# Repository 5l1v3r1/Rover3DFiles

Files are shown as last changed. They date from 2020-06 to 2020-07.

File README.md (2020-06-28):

<p align="justify"><b>
<font size="2">Tanım</font></b><font size="2"><br>
Bu bölümde projenin bir parçası olan, İnternet üzerinden kontrol edilecek ve üzerinde çeşitli görev yükü bulunacak olan model Mars Rover'a ait 3D yazıcı dosyaları yer almaktadır.
</font></p>
<p align="justify"><b><font size="2">Malzeme<br>
</font></b><font size="2"> Malzeme olarak istenilen renkte filament kullanılabilir. Çalışmalarda kullanılan filament türü PLA'dır. Dosyalar 180-220 Nozzle, 55-60 tabla sıcaklığında, %7 doluluk oranında basılabilir. Yüklenmiş/yüklenecek dosyalar *.stl formatında olup, kendi 3D yazıcınıza uygun bir 
dilimleyici programı kullanarak G-Code üretebilirsiniz. Kabin ve amortisör sistemleri destekli baskıya ihtiyaç duymaktadır.</font></p>

----------------------------------------------------------------

<b>Description: </b>

This section includes 3D printer files of the Mars Rover model, which will be controlled over the Internet and will have various tasks. 

<b>Materials: </b>

As a printing material, any preferred color of filament can be used. The type of filament used in the this project is PLA. Files can be printed with 180-220 Nozzle, 55-60 bed temperature, 7% fullness ratio. Files, which are already uploaded or will be uploaded, will be in *.stl format. So it will be possible to create G-Code suitable for your 3D printer by using an appropriate slicing program. Cabin and dashpot systems need supported printing.

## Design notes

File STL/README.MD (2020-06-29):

<p align="justify"><font size="2">
<b>Tekerlekler</b><br>
6 Adet yüzeyine tutunma çıkıntıları 
eklenmiş, 5 adet jant bağlantılı destek parçasına sahip, 100 mm çapında 
tekerlerden oluşmaktadır. Bir tekerin baskı süresi genel tip yazıcılarda 
yaklaşık olarak 6,5 saattir, toplamda teker başına yaklaşık 14.8 metre 44 gram 
filament harcanmaktadır. Teker mili yuvası standart 6V 250 RPM plastik dişli çift 
şaftlı motorlar için uygundur. Yapıştırma desteği için 1 mm esnek pay 
bırakılmıştır.</font></p>
<p align="justify"><b><font size="2">Tutucular</font></b><font size="2"><br>
Ana gövde ile tekerlek sistemini birleştiren kare 
şeklindeki parçadır. Rover üzerinde 3 adet bulunmaktadır. Bu malzemenin görevi; 
rover'e modüler bir yapı kazandırarak istenildiği gibi uzunluğun ve kullanım 
hacminin değiştirilmesine olanak sağlamak, farklı çap teker yapısının kolayca 
değiştirilebilmesine olanak sağlamaktır.&nbsp; Yaklaşık olarak 1 saat 23 dakika 
baskı süresinde 4 metre 12 gram filament&nbsp;harcanmaktadır.&nbsp;&nbsp;&nbsp; </font>
</p>
<p align="justify"><b><font size="2">Salıncak</font></b><font size="2"><br>
Tutucu, amortisör ve motor yatağı ile birlikte 
kullanılan ve teker yapısına arazinin durumuna göre dikey eksende esnek hareket 
sağlayan yapıdır. Rover üzerinde 6 adet yer almaktadır.</font></p>
<p align="justify"><b><font size="2">Amortisörler<br>
</font></b><font size="2">Aracın engebeli arazide sürüş stabilitesini arttırmak amacıyla 
kullanılan sistemdir. Yay sertliği ve malzemesi kullanıcı tarafından 
ayarlanabilir. Sistem iki adet birbirinin içine geçen parçadan oluşmaktadır, 
rover üzerinde toplamda 6 adet amortisör takımı vardır. Amortisör başına 
yaklaşık olarak 4 dakika baskı süresinde 1.51 metre 5 gram filament harcanmaktadır.</font></p>
<p align="justify"><font size="2"><b>Motor Yatağı</b><br>
Plastik dişli motoru sabitleyen ve taşıyan ve salıncağa bağlanan parçadır. 
Yaklaşık olarak 57 dakika baskı süresinde, 2,30 metre 7 gram filament harcanmaktadır. Parçanın destekli basılması önerilir.</font></p>

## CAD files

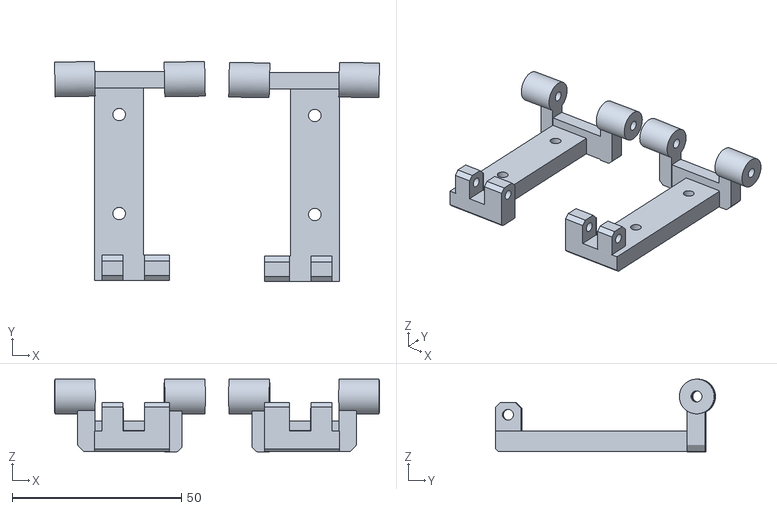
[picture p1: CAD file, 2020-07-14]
STL/Salincak-Suspensionx2-L-R.stl
96.0 x 65.0 x 21.5

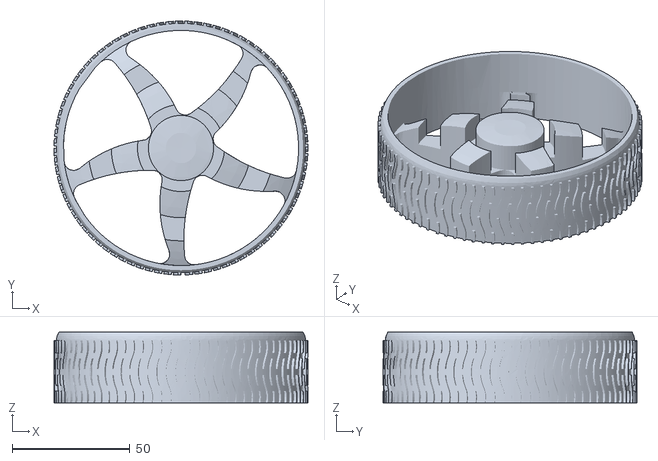
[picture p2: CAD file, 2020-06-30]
STL/Teker_Sol_Wheel_Right.stl
108.0 x 108.0 x 30.0

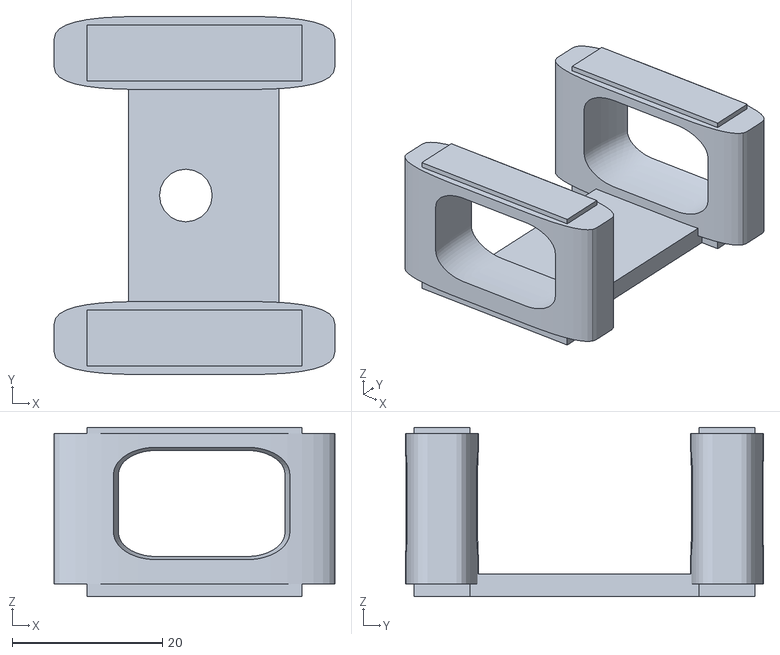
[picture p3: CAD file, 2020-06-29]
STL/Sensor_Tutucu_Sensor_Holder.stl
37.3 x 47.6 x 22.5

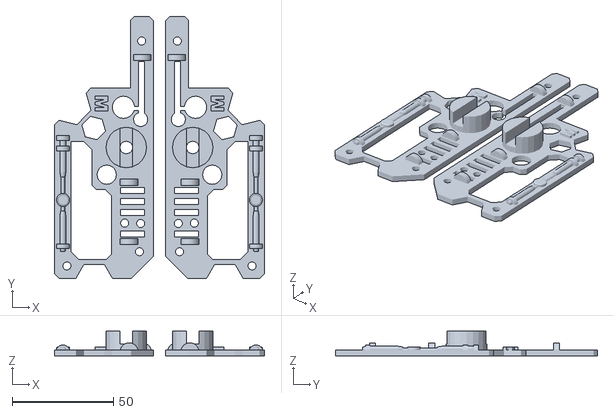
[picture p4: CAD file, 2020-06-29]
STL/Beacon_Left-Right_Side.stl
103.8 x 129.3 x 12.3

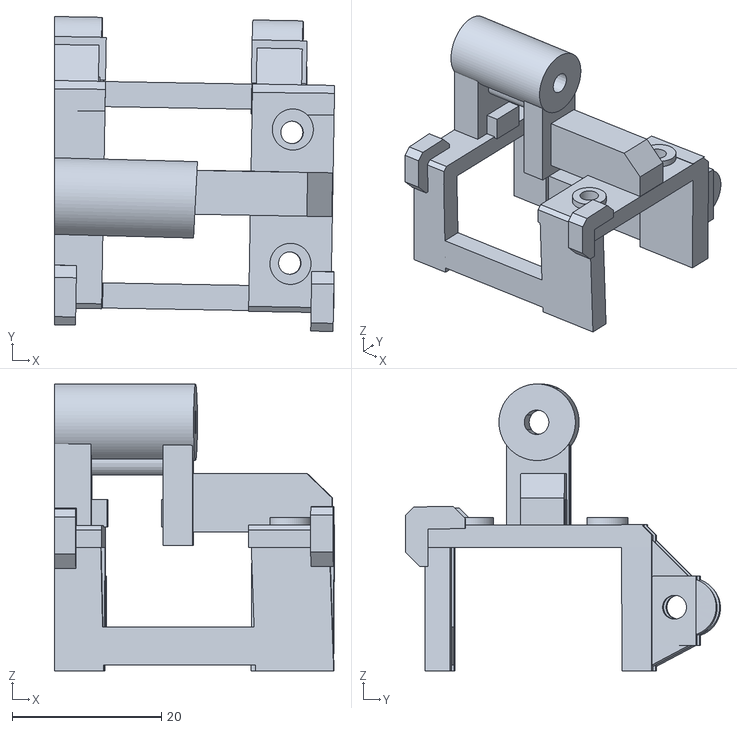
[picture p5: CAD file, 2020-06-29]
STL/Suspansiyon_1_Suspension_Part_1_Right.stl
37.5 x 42.2 x 38.4

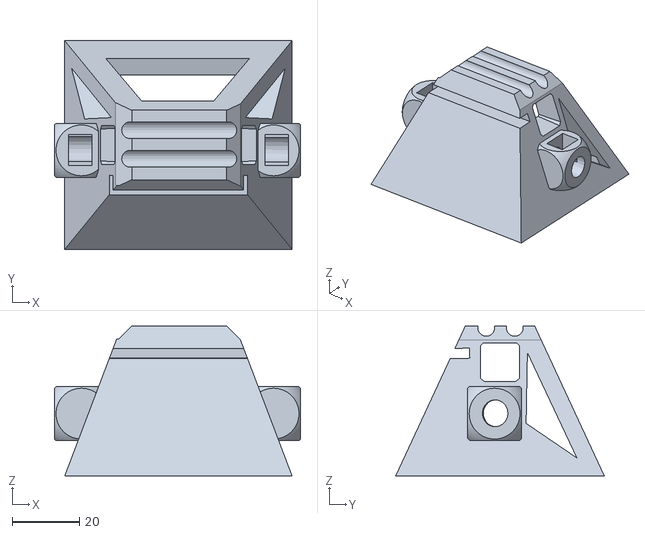
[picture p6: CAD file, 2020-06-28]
STL/Gorev_Kabini_Crew_Area.stl
73.1 x 62.0 x 44.5

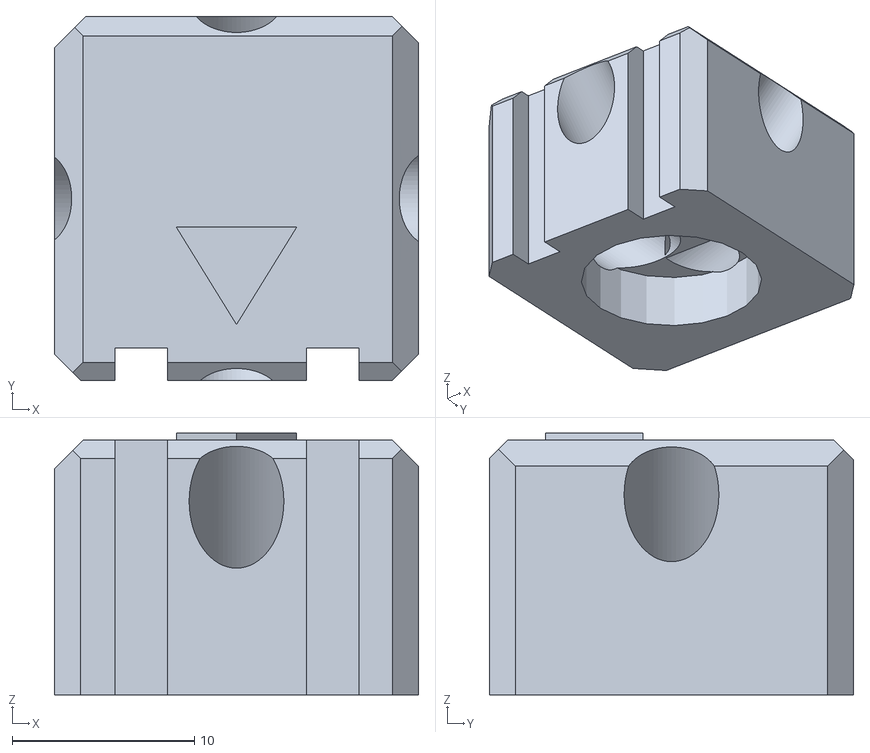
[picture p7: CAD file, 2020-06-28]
STL/Nadir_Sensor.stl
20.0 x 20.0 x 14.4

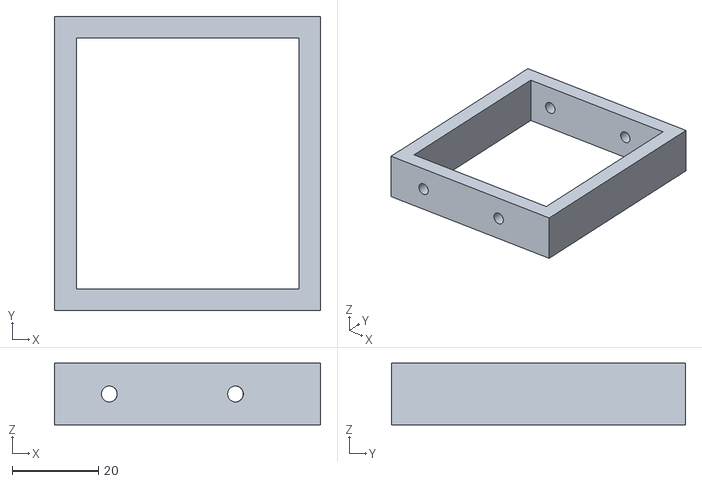
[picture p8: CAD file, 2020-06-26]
STL/Amortisor_Tutucu_Shock_Absorber_Holder.stl
61.7 x 68.3 x 14.3

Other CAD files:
STL/Teker_Sol_Wheel_Left.stl
STL/Suspansiyon_1_Suspension_Part_1_Left.stl

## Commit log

2020-06-26 Yeni dizayn
    [Amortisor_Tutucu_Shock_Absorber_Holder.stl, Suspansiyon_1_Suspension_Part_1.stl, Suspansiyon_2_Suspension_Part_2.stl]
2020-06-27 İkinci şaft çıkışı hatası
    İkinci şaft çıkışını ara parçaya temas ettiği için yeni güçlendirme çalışması yapılacak amacıyla silindi.
    [Suspansiyon_1_Suspension_Part_1.stl]
2020-06-28 Nadir Sensor
    4 adet LDR destekli Nadir sensör. 3D yazıcıda desteksiz basılabilir versiyon.
    [Nadir_Sensor.stl]
2020-06-28 Ön kısım - Görev Kabini
    Destekli baskı gereklidir. Ana tutucu parçaya yapıştırılarak kullanılmalı. Kanallı ön alt kısma ön aydınlatma parçası yapıştırılabilir.
    [Gorev_Kabini_Crew_Area.stl]
2020-06-29 Sol ve Sağ Suspansiyon (Left/Right Suspension)
    [Suspansiyon_1_Suspension_Part_1_Left.stl, Suspansiyon_1_Suspension_Part_1_Right.stl]
2020-06-29 Yan yüzel beacon yüzey parçası
    Sol ve sağ iki parça.
    [Beacon_Left-Right_Side.stl]
2020-06-29 Sensör tutucu
    Arka üst sensör tutucu versiyon 1.
    [Sensor_Tutucu_Sensor_Holder.stl]
2020-06-30 Tek yön teker .z
    Yeniden dizayn edilip sol ve sağ olarak iki ayrı teker ekleneceği için
    [Teker_Wheel.stl]
2020-06-30 Yeni dizayn
    Teker tutucu yüzeyleri sol ve sağ yan için yeniden düzenlendi.
    [Teker_Sol_Wheel_Left.stl, Teker_Sol_Wheel_Right.stl]
2020-07-14 Yeni çizim eklenecek
    Sağ ve sol olarak yenisi ekleneceği için silindi.
    [Suspansiyon_2_Suspension_Part_2.stl]
2020-07-14 Yeni Dizayn (New design part X2)
    Sağ ve sol parça olarak yeniden eklendi. (It has been added as a left and right piece.)
    [Salincak-Suspensionx2-L-R.stl]
